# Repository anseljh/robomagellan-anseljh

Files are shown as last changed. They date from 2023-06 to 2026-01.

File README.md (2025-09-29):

# robomagellan-anseljh

This repo has notes, code, and other stuff related to my work toward competing in a Robo-Magellan contest. I plan to do at least the [TableBot challenge](https://github.com/anseljh/tablebot) first, but I've started planning and collecting parts for Robo-Magellan. I hope to be ready to compete in spring/summer 2024, but that may be overly ambitious. 2025 for sure!

## Robo-Magellan

> Robo-Magellan is a robotics competition emphasizing autonomous navigation and obstacle avoidance over varied, outdoor terrain. Robots have three opportunities to navigate from a starting point to an ending point and are scored on time required to complete the course with opportunities to lower the score based on contacting intermediate points.

- RoboGames [Robo-Magellan Rules](http://robogames.net/rules/magellan.php)
- Seattle Robotic Society Robothon [Robo-Magellan Rules](https://robothon.org/rules-robo-magellan/)

## Design Considerations

- **Size**: The robot will need to be able to overcome some terrain obstacles, so it shouldn't be too small or underpowered.
- **Sensors**:
  - GPS (navigation)
  - Compass (navigation; don't want to rely on GPS just to get heading)
  - Camera (to detect cones)
  - Distance sensors of some kind (collision avoidance)
  - Lidar (to detect cones; collision avoidance; also just cool)
  - Tactile sensors (to detect contact with cones)
- **Compute**:
  - Something powerful enough to process images from the camera and identify orange cones. I have a Raspberry Pi Model 3 A+ which I'll try out. It may be underpowered (only 512 GB RAM).
  - Planning to base the rest around an RP2040 board, probably one of my Raspberry Pi Picos. Could I just use the more powerful Raspberry Pi computer? Probably, but, among other considerations, I think it's more funny to make the computer be a peripheral for the microcontroller.
- **Dead man's switch**: The Robo-Magellan rules require the operator be able to stop a robot immediately by letting go of a switch. I have a few ideas about this, but nothing definitive. I might use the [RFM69HCW packet radios](https://www.sparkfun.com/products/12775) that I've used before and have a remote send a heartbeat to the robot while a button is pressed, and if that signal doesn't come, a relay cuts off power to the motors. I want to research how other people are doing this and maybe not reinvent the wheel. There's a Sparkfun tutorial called [How to Build a Remote Kill Switch](https://learn.sparkfun.com/tutorials/how-to-build-a-remote-kill-switch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) that is very similar to my concept.
- **Logging**: I'll want to log data for later analysis. I got an SD card breakout board for this that I haven't tried out yet. On the other hand, I might want to use that for quickly delivering GPS coordinates to the bot. Might need to get a second one in that case.

## Intermediate Milestones

1. **Do a working [TableBot](https://www.hbrobotics.org/index.php/challenges/).** Work on fundamentals in a small form factor. Complete a project of some complexity with CircuitPython. Fun!
1. **Make the remote.** Decide on the dead-man's switch mechanism. Design the PCB for the remote. Get it fabricated. Add panel-mount holes to an enclosure, including a port for the Wii Nunchuck. Attach all the things! Test it with the TableBot.
1. **Get the big DC motors running.** This entails working out all the power management for the motors, and hooking up the motor driver.
1. **Test remote motor power cut-off.** Need to verify this works before getting too far along with everything else.
1. **Figure out how to mount wheels to the big DC motors.** I'm even more of a rookie when it comes to mechanical engineering. Lots to learn here.
1. **Build a chassis.** Figure out how big & what kind of chassis to build. Build it.
1. **Do a working [FloorBot](https://www.hbrobotics.org/index.php/challenges/).** This is another good intermediate goal. I can use the same chassis, motors, remote, etc., but not have to worry about GPS, terrain, and recognizing orange cones yet.

## Parts Selection

### Motors

I got four chunky motors at a [Homebrew Robotics Club](hbrobotics.org/) meeting in early 2023. It's been a bit challenging to pin down precisely what they are, but I *think* they are [RAE M1500 permanent magnet DC motors](http://raemotors.com/products/motors/dc-motors/m1500-series/m1500.php) with [G211 right-angle gearmotors](http://raemotors.com/products/motors/gearmotors/right-angle/g211-series.php). Here are the basic specifications. I think they'll do the job.

- Voltage: 18V
- Current: 2A
- Speed: 200 rpm
- Torque: 6 in.-lb.
- Weight: Unknown. Need to weight them. Heavy!

### Battery & Power Distribution

Those motors will need a good amount of power. So far, I think I'll use a small-ish SLA battery. You can get one for about $20. I'll then need to step up the power from 12V to 18V, so I got a [Pololu 4.5-20V Fine-Adjust Step-Up Voltage Regulator U3V70A](https://www.pololu.com/product/2890).

### Chassis

I haven't thought about the chassis much yet. It needs to be able to hold these heavy motors and the SLA battery, which itself is 4.5 pounds.

### Motor Driver

The little motor drivers I've used before won't cut it for driving multiple 18V 2A motors, so I needed to get a beefier driver. I settled on the [Cytron 10A 5-30V Dual Channel DC Motor Driver](https://www.robotshop.com/products/cytron-10a-5-30v-dual-channel-dc-motor-driver?variant=42358540009633). I considered the very cool [RoboClaw](https://www.basicmicro.com/motor-controller) as shown in [Camp Peavy's book *HomeBrewed Robots!*](https://www.amazon.com/HomeBrewed-Robots-Camp-Peavy/dp/B0BW283Q27), but it's expensive and a bit more complex than I need. (I think.)

### Wheels, et cetera

I need to figure out how to mount wheels to the motor shafts, which are 1/4" diameter. I don't know much about this part. It seems to be hard to find wheel hubs for 1/4" diameter shafts, but there's probably stuff I'm missing.

### GPS

Thanks to a thread on the [Homebrew Robotics Club mailing list](https://groups.google.com/g/hbrobotics/about), I scored a GPS module for $9. It's the [HiLetgo GY-NEO6MV2](https://www.amazon.com/gp/product/B01D1D0F5M). It's not the best thing ever, but it works, and did I mention that it was $9? It uses a [Ublox NEO-6M](https://www.u-blox.com/en/product/neo-6-series) GPS module. It's 3V compatible and you just communicate to it over a UART. There's a [CircuitPython GPS library](https://docs.circuitpython.org/projects/gps/en/latest/) that works great. It takes several minutes to warm up (or whatever it's doing) but once that's done, it works fine.

### Lidar

I have a [getSurreal XV Lidar Sensor Mount Package](https://www.getsurreal.com/product/xv-lidar-sensor-mount-package/), which uses the lidar sensor from a Neato XV robotic vacuum.

The controller is the [getSurreal Lidar Controller v2.0](https://www.getsurreal.com/product/lidar-controller-v2-0/).

I had to get a replacement [drive belt](https://www.amazon.com/dp/B08KFNRXXV) for the motor that spins the laser around. ($9.95)

### Distance sensors

In addition to the lidar, I'm planning to add a few other distance sensors around the bot for further collision avoidance redundancy, in case something goes wrong with the lidar. I'm not sure yet how many distance sensors I want, or what type to use.

I have a trusty HC-SR04 ultrasonic sensor which uses 5V, as well as a 3.3V equivalent [RCWL-1601](https://www.adafruit.com/product/4007). These will probably work OK, but I'll need to test. I may need to get more depending on what kind of coverage I want.

[My TableBot](https://github.com/anseljh/tablebot) is using some [little infrared sensors](https://www.amazon.com/dp/B07W97H2WS) for detecting the edge of the table, but I doubt they'll be good for this application.

### Compute

I'd like to primarily use a Raspberry Pi Pico. The Pico is a cool little board based on the RP2040 microcontroller chip. I've been programming these in [CircuitPython](https://circuitpython.org/), and it is tons of fun.

There are two tasks that will require more compute power than the little Pico can muster, so I'm planning to use a beefier single-board computer for those tasks, and send their outputs to the Pico. So far I intend to use a Raspberry Pi Model 3 A+. It will process camera images to find the target cones, and send its conclusions to the Pico.

### Logging

I'll log telemetry to a micro SD card. I have a breakout board for that.

Should there be a realtime clock? Might not need one because we can [get time from the GPS](https://docs.circuitpython.org/projects/gps/en/latest/examples.html#time-source).

## Bills of Materials

### Control Board

- [ ] Custom PCB
- [x] Raspberry Pi Pico - $4
- [x] [RFM69HCW packet radio](https://www.sparkfun.com/products/12775) to receive dead-man's switch signal (autonomous mode) and commands from remote (manual mode) - $14
- [x] Antenna - $1
- [x] SMA antenna connector
- [ ] Toggle switch for autonomous/manual mode selection
- [ ] LEDs for autonomous/manual mode indication
- [x] Speaker for auditory output
- [x] GPS module: [HiLetgo GY-NEO6MV2](https://www.amazon.com/gp/product/B01D1D0F5M) - $9
- [x] Magnetometer (compass): [Sparkfun Micromag 3-axis magnetometer](https://www.sparkfun.com/products/retired/244) - $15.49 on eBay
- [x] [Micro SD card breakout board](https://www.adafruit.com/product/4682) for logging - $3.50
- [ ] Second [Micro SD card breakout board](https://www.adafruit.com/product/4682) for GPS coordinates - $3.50
- [ ] Bump switch for cone touch detection
- [x] 2x connectors for data from optical encoders (TE Connectivity part no. [3-640442-5](https://www.te.com/usa-en/product-3-640442-5.html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)) - $1.08
- [x] [MCP23008](https://www.adafruit.com/product/593) I2C GPIO expander - $1.95

### Motors and Drive System

- [x] 2x [RAE M1500 permanent magnet DC motors](http://raemotors.com/products/motors/dc-motors/m1500-series/m1500.php) with [G211 right-angle gearmotors](http://raemotors.com/products/motors/gearmotors/right-angle/g211-series.php) - free
- [x] 2x [Broadcom HEDM-5600#J06 optical encoders](https://www.broadcom.com/products/motion-control-encoders/incremental-encoders/transmissive-encoders/hedm-5600j06) - *requires 5V* - free
- [x] [Cytron 10A 5-30V Dual Channel DC Motor Driver](https://www.robotshop.com/products/cytron-10a-5-30v-dual-channel-dc-motor-driver?variant=42358540009633) - $23.50

### Power Systems

- [x] 12V SLA battery, like this [Mighty Max 12V 7 Ah SLA battery](https://www.homedepot.com/p/MIGHTY-MAX-BATTERY-12-Volt-7-Ah-Sealed-Lead-Acid-SLA-Rechargeable-Battery-ML7-12/307979135). It weighs 4.5 pounds. - $20
- [x] [Pololu 4.5-20V Fine-Adjust Step-Up Voltage Regulator U3V70A](https://www.pololu.com/product/2890): I'll use one of these to step up the 12V from the SLA battery to 18V to the motors. ([Bought from RobotShop](https://www.robotshop.com/products/pololu-45-20v-fine-adjust-step-up-voltage-regulator-u3v70a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)) - $40.95
- [x] Mini fuse holder: [Littelfuse FHM2BP](https://www.oreillyauto.com/detail/c/blister-pack/littelfuse-blister-pack-fuse-holder/lit3/fhm2bp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) - $4.99
- [x] 5A mini fuse: [Littelfuse 5 Amp Fuse MIN5BP](https://www.oreillyauto.com/detail/c/blister-pack/littelfuse-blister-pack-5-amp-fuse/lit3/min5bp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) - $5.29 for 5
- [ ] Big red button for emergency stop
- [ ] Toggle switch for control board power
- [ ] Toggle switch for manual motor power enable/cutoff
- [ ] Relay for motor power control
- [ ] Battery for control board
- [ ] 2x USB to micro-USB cable
  - Battery to Raspberry Pi 3 power
  - Raspberry Pi 3 to lidar controller

### Camera/Lidar System

- [x] Raspberry Pi Model 3 A+ - $25
- [x] Random old webcam (If it doesn't work well enough, get a Raspberry Pi Camera Module)
- [ ] Micro-USB cable from battery
- [x] [getSurreal Lidar Controller v2.0](https://www.getsurreal.com/product/lidar-controller-v2-0/) and [Mount Package](https://www.getsurreal.com/product/xv-lidar-sensor-mount-package/) with Neato XV lidar sensor

### Remote & Dead-Man's Switch

For the safety stop mechanism, I'm envisioning a small handheld device that will double as a remote control when moving the robot manually.

- [ ] Custom PCB
- [x] Raspberry Pi Pico - $4
- [x] [RFM69HCW packet radio](https://www.sparkfun.com/products/12775) - $14
- [x] Antenna - $1
- [x] SMA antenna connector
- [x] [Adafruit Wii Nunchuck Breakout Adapter](https://www.adafruit.com/product/4836) - $2.95
- [x] Wii Nunchuck
- [ ] Big button for dead-man's switch
- [ ] Toggle switch for power
- [ ] Enclosure (I have a few that might work)
- [ ] Green LED for connection indicator
- [ ] Red LED for heartbeat blink
- [ ] Another LED for mode indicator?

## Pins Required

### Control Pico

- 2 for UART to Pi 3
- 2 for UART to GPS module
- SPI (4) + 1 = **5** for radio
- SPI (3 reused + 1 CS) + 2 = **3** for magnetometer
- SPI (reuse 3 + 1 CS) + 1 = **2** for [Adafruit Micro SD SPI or SDIO Card Breakout](https://www.adafruit.com/product/4682)
- SPI (reuse 3 + 1 CS) + 1 = **2** for second SD card breakout
- 2x2 = **4** for optical encoders
- 1 for mode selection switch
- 1 for mode selection LED
- 1 for speaker
- 1 for bump switch
- 1 for motor power relay
- 4 for motor driver

Total: **29**

Uh-oh; there are only 26 usable GPIO pins on the Pico. We'll have to offload some of this to an IO expander. I have both an [MCP23008](https://www.adafruit.com/product/593) and an [MCP23017](https://www.adafruit.com/product/732) for that (I2C to 8 or 16 GPIO, respectively).

### Raspberry Pi 3

- 2 for UART to Pico

Total: **2**

### Remote Pico

- 1 for dead-man's switch
- 5 for radio
- 2 for I2C to Nunchuck breakout board
- 3 for indicator LEDs

Total: **11**

## Block Diagram

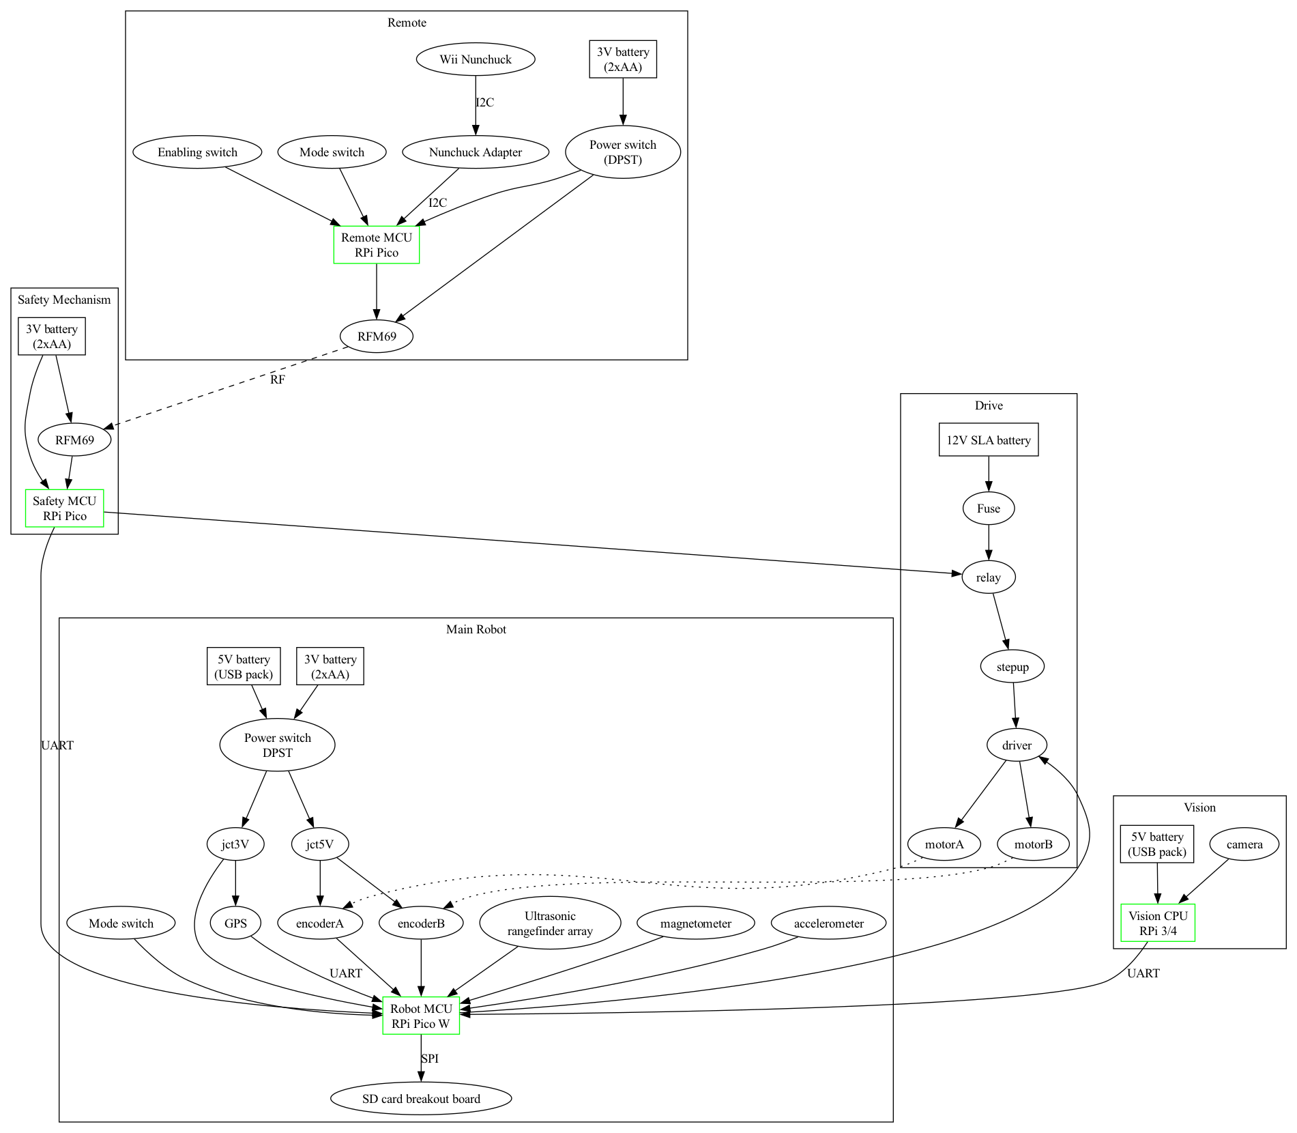
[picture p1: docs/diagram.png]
Diagram of systems and components


Rendered with [Graphviz](https://graphviz.org/) from `docs/diagram.dot` with:

```shell
dot -Tpng docs/diagram.dot > docs/diagram.png
```

## Software used

- [Graphviz](https://graphviz.org/) for block and state diagrams
- [LibreCAD](https://librecad.org/) for 2D CAD drawings, mainly for drilling templates for the chassis

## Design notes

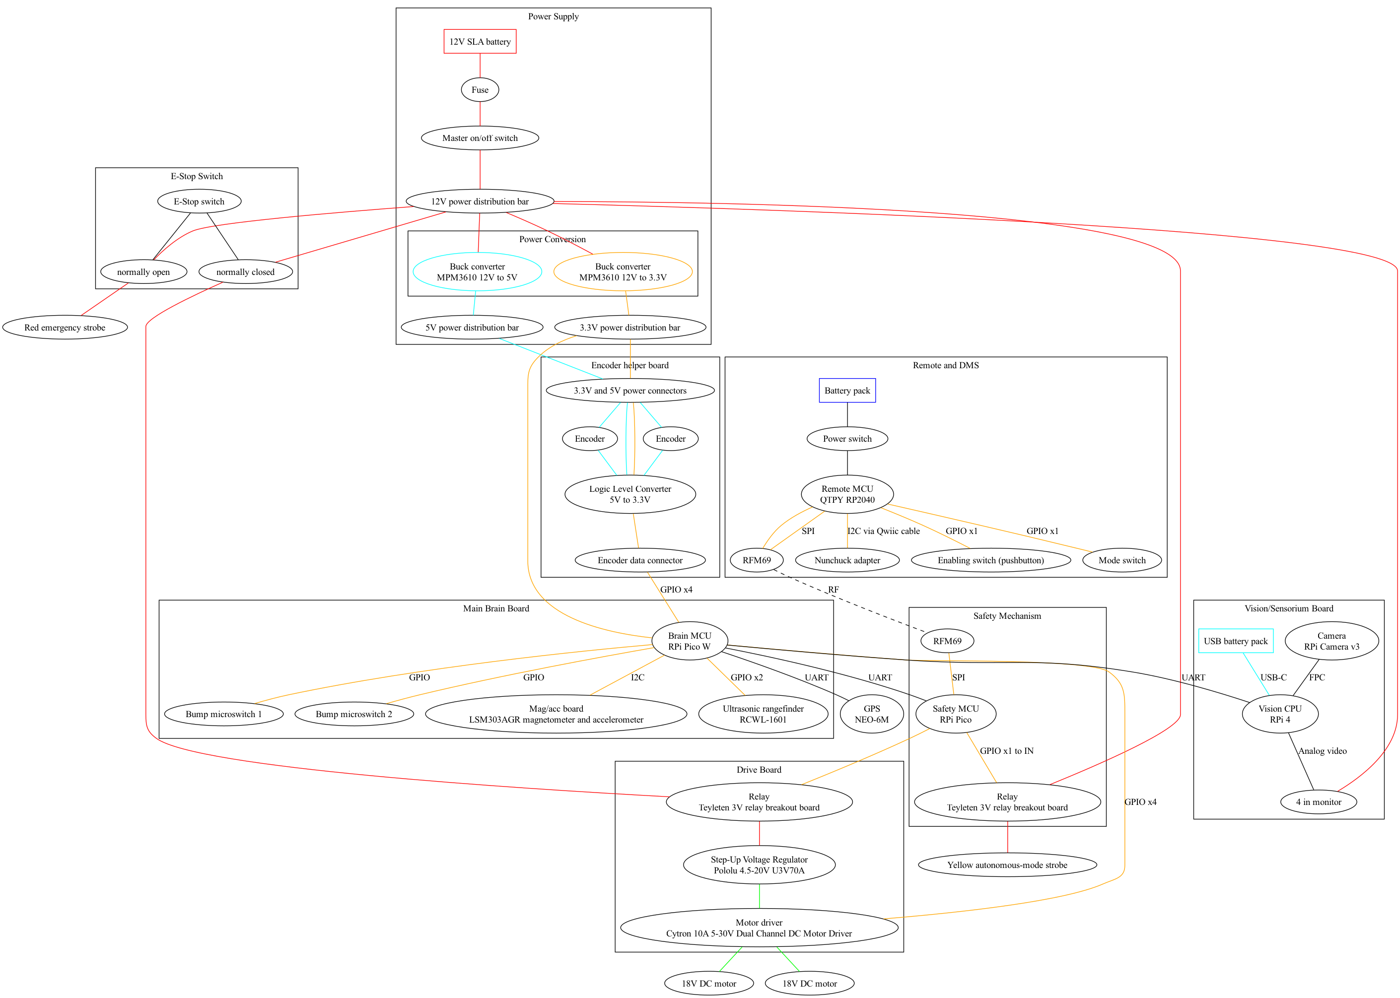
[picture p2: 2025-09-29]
docs/clanker-hardware.png

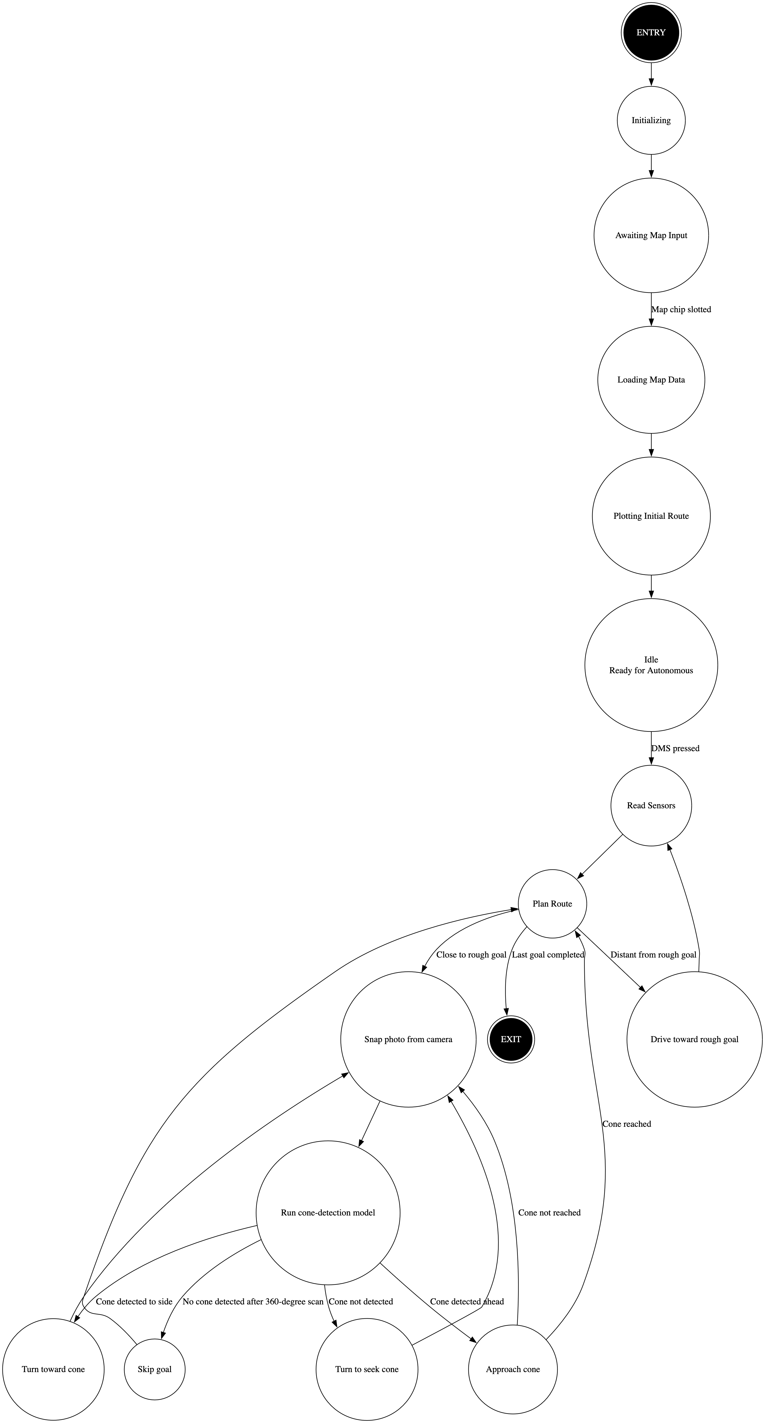
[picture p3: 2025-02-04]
docs/states.png

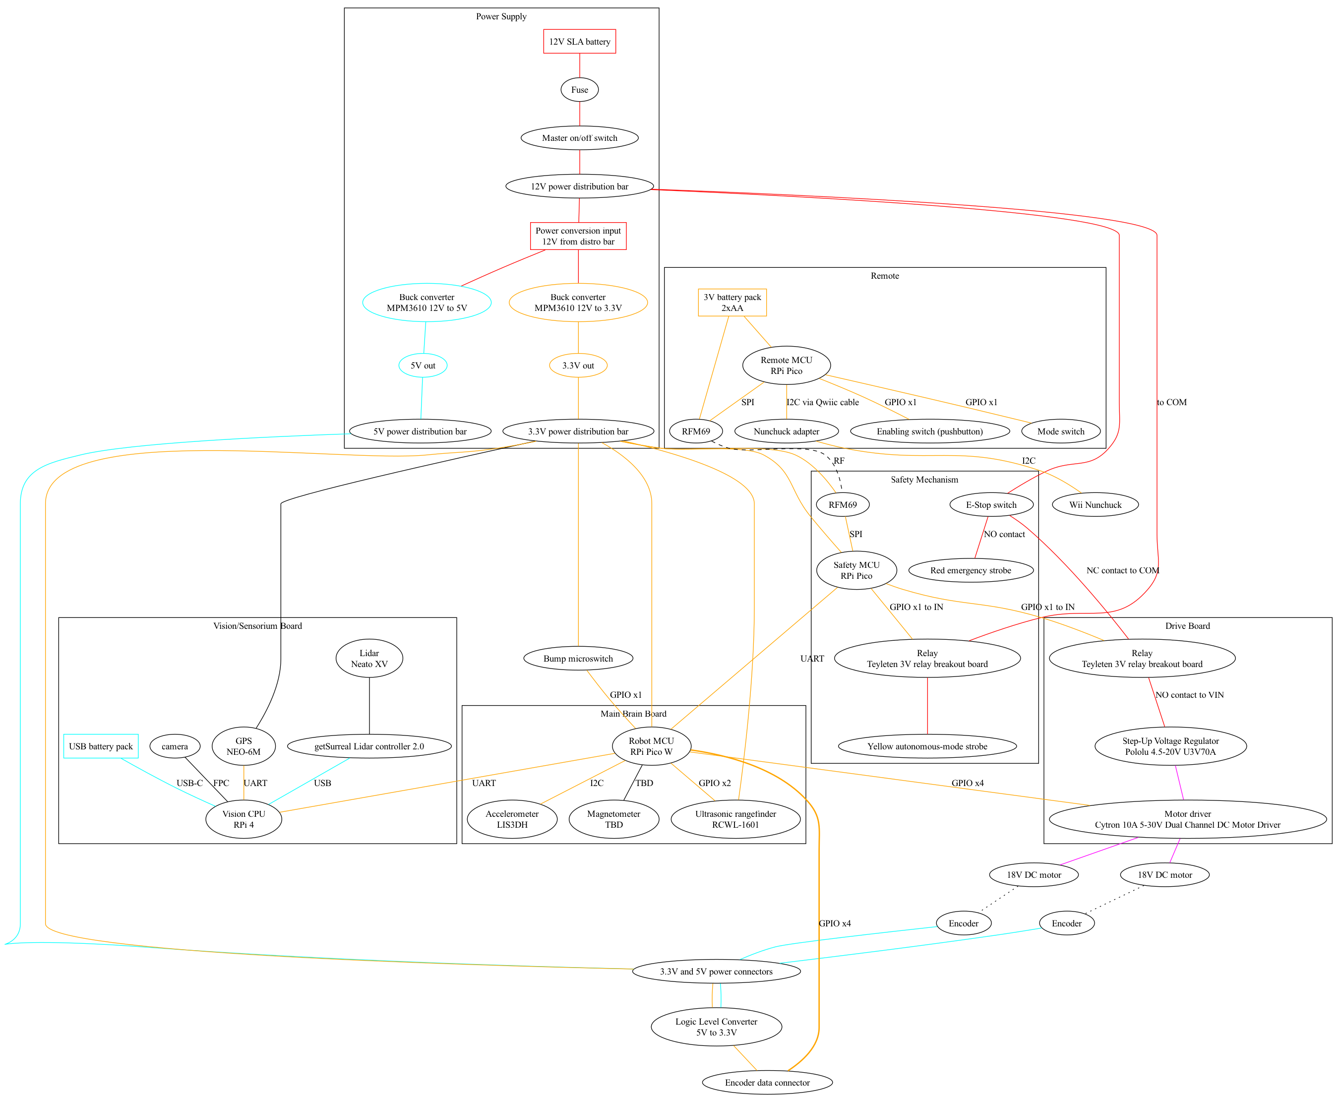
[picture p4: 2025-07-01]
docs/diagram3.png

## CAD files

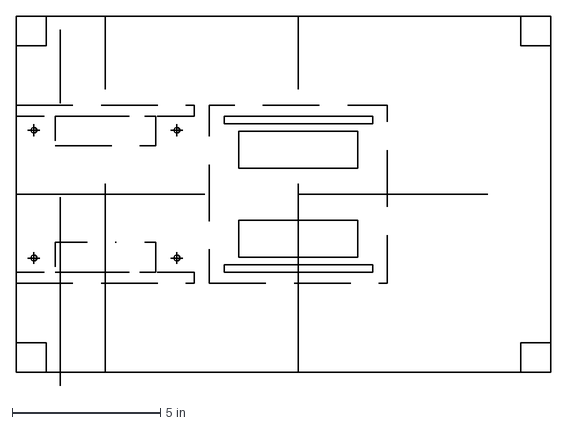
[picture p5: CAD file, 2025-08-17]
CAD/Lower MDF board.dxf
18.0 x 12.5 in

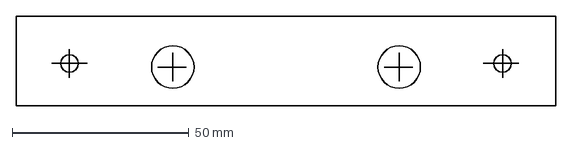
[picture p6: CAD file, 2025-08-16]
CAD/Bearing mount bar.dxf
152.4 x 25.4 mm

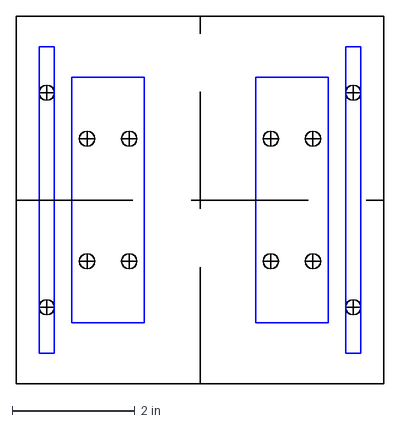
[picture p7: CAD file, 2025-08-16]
CAD/Motor mount plate.dxf
6.00 x 6.00 in

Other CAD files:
CAD/Empty template.dxf

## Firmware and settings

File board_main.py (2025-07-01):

"""
CircuitPython code for the main robot MCU.
Board: Raspberry Pi Pico W

Devices:
- Serial to safety board (hardware UART)
- Serial to vision RPi 4 (hardware UART)
- Serial to GPS module (PIO UART)
- (maybe) Serial to Neato lidar (PIO UART)
- Motor controller (4 GPIO pins)
- Mode selector switch (1 GPIO)
- Wifi network selector DIP switch (1 GPIO)
- Some status LEDs TBD (1 GPIO each)

Pinout diagram: https://picow.pinout.xyz/
"""

import time
import board
import pwmio
import digitalio
import busio

from utils import init_hw_uart, init_pio_uart
from robot import RoboMagellanBot

# Pin setup
MODE_SELECTOR_PIN = None # mode-selector switch (manual / autonomous)
AUTONOMOUS_LAMP_PIN = None # bright yellow light or strobe to indicate autonomous mode is active
VISION_TX_PIN = None
VISION_RX_PIN = None
GPS_TX_PIN = None
GPS_RX_PIN = None
LIDAR_TX_PIN = None
LIDAR_RX_PIN = None
M1_PWM_PIN = None
M1_DIR_PIN = None
M2_PWM_PIN = None
M2_DIR_PIN = None
QWIIC_SCL = None
QWIIC_SDA = None

class Motor:
    FORWARD = 1
    BACKWARD = -1
    
    def __init__(self, pwm_pin, dir_pin, motor_dir=FORWARD):
        self.pwm = pwmio.PWMOut(pwm_pin, frequency=1000, duty_cycle=0)
        self.dir = digitalio.DigitalInOut(dir_pin)
        self.dir.direction = digitalio.Direction.OUTPUT

    def set_speed(self, speed):
        if speed < 0:
            self.dir.value = True
            self.speed = -speed
        else:
            self.dir.value = False
            self.speed = speed
        
        # Flip direction if motor is facing opposite
        if self.motor_dir == Motor.BACKWARD:
            self.dir.value = not self.dir.value
        
        self.pwm.duty_cycle = int(self.speed * 65535)
    
    def stop(self):
        self.pwm.duty_cycle = 0

class Drivetrain:
    def __init__(self, M1_PWM_PIN, M1_DIR_PIN, M2_PWM_PIN, M2_DIR_PIN):
        self.motor_left = Motor(M1_PWM_PIN, M1_DIR_PIN, Motor.FORWARD)
        self.motor_right = Motor(M2_PWM_PIN, M2_DIR_PIN, Motor.BACKWARD)
        self.stop()
        print("Drivetrain reporting for duty!")

    def stop(self):
        self.motor_left.stop()
        self.motor_right.stop()
    
    def turn_left(self, speed):
        self.motor_left.set_speed(-speed)
        self.motor_right.set_speed(speed)

    def turn_right(self, speed):
        self.motor_left.set_speed(speed)
        self.motor_right.set_speed(-speed)
    
    def forward(self, speed):
        self.motor_left.set_speed(speed)
        self.motor_right.set_speed(speed)

    def backward(self, speed):
        self.motor_left.set_speed(-speed)
        self.motor_right.set_speed(-speed)
    
    def test_partern(self):
        self.stop()
        
        # TODO: Honk
        time.sleep(1)
        
        self.turn_right(0.25)
        time.sleep(1)
        self.stop()
        time.sleep(1)
        
        self.turn_left(0.25)
        time.sleep(1)
        self.stop()
        time.sleep(1)
        
        self.forward(0.25)
        time.sleep(1)
        self.stop()
        time.sleep(1)
        
        self.backward(0.25)
        time.sleep(1)
        self.stop()
        
        # TODO: Honk

class MainBoard:

    def __init__(self):
        # UART from safety MCU for conveying non-safety commands from remote
        self.uart_safety = init_hw_uart(board.TX, board.RX)

        # UART for cone prediction from RPi 4
        self.uart_vision = init_pio_uart(VISION_TX_PIN, VISION_RX_PIN)

        # UART for GPS module
        self.uart_GPS = init_pio_uart(GPS_TX_PIN, GPS_RX_PIN)
        
        # UART for Neato lidar
        # self.uart_lidar = None # TODO: setup a PIO UART for the Neato lidar
        # self.uart_lidar = init_pio_uart(LIDAR_TX_PIN, LIDAR_RX_PIN)

        # Initialize drivetrain
        self.drivetrain = Drivetrain()

        # Init mode selector switch
        # TODO

        # Init I2C bus for Qwiic devices
        i2c1 = busio.I2C(QWIIC_SCL, QWIIC_SDA)

        self.bot = RoboMagellanBot()

    def main_loop():
        pass

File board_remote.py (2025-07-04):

"""
CircuitPython code for the remote MCU.
Board: Adafruit QT PY RP2040
    https://circuitpython.org/board/adafruit_qtpy_rp2040/

Devices:
- RFM69 radio (SPI)
- Nunchuk adapter (I2C)
- Dead-man's switch button (1 GPIO)
- Autonomous/manual selector switch (1 GPIO)
- Autonomous-mode LED (1 GPIO)

Sparkfun: How to Build a Remote Kill Switch
    https://learn.sparkfun.com/tutorials/how-to-build-a-remote-kill-switch
"""

import time
import board
import busio
from digitalio import DigitalInOut, Direction, Pull

from adafruit_nunchuk import Nunchuk

from utils import init_radio

# Pin setup
PIN_MOSI = board.GP3
PIN_MISO = board.GP4
PIN_SCK = board.GP6
PIN_CS = board.GP5
PIN_RESET = board.GP20
QWIIC_SCL = board.GP23
QWIIC_SDA = board.GP22
SWITCH_DEAD_MAN = board.A0  # A0 for enabling/dead-man's switch
SWITCH_MODE = board.A1  # A1 for autonomous/manual mode switch
# nothing on A2 yet
LED_MODE = board.A3  # A3 for autonomous/manual mode LED


class RemoteBoard:
    def __init__(self):
        # Init mode LED
        self.led_mode = DigitalInOut(LED_MODE)
        self.led_mode.direction = Direction.OUTPUT
        print("Mode LED initialized.")

        # Init mode switch
        self.switch_mode = DigitalInOut(SWITCH_MODE)
        self.switch_mode.direction = Direction.INPUT
        # self.switch_mode.pull = None  # Pull.UP  # Pull-up resistor for switch
        print("Mode switch initialized.")

        # Init dead-man's switch
        self.switch_enabling = DigitalInOut(SWITCH_DEAD_MAN)
        self.switch_enabling.direction = Direction.INPUT
        # self.switch_enabling.pull = Pull.UP
        print("Dead-man's switch initialized.")

        # Init RFM69 radio
        self.radio = init_radio(
            mosi_pin=PIN_MOSI,
            miso_pin=PIN_MISO,
            clock_pin=PIN_SCK,
            cs_pin=PIN_CS,
            reset_pin=PIN_RESET,
        )
        print("RFM69 radio initialized.")
        print(self.radio)
        print(f"Temperature: {self.radio.temperature}C")
        print(f"Frequency: {self.radio.frequency_mhz} MHz")
        print(f"Bit rate: {self.radio.bitrate / 1000} kbit/s")
        print(f"Frequency deviation: {self.radio.frequency_deviation} Hz")

        # Instantiate Nunchuck
        i2c1 = busio.I2C(QWIIC_SCL, QWIIC_SDA)
        try:
            self.nunchuck = Nunchuk(i2c1)
            print("Nunchuk initialized.")
            print(self.nunchuck)
        except ValueError as e:
            print(f"Failed to initialize Nunchuk: {e}")
            self.nunchuck = None
        
        print("** Remote board initialized **")

    def main_loop(self):
        print("Remote main loop beginning...")
        while True:
            if self.switch_mode.value:
                print("Mode switch is HIGH")
                self.led_mode.value = True
                print("Autonomous mode active.")
            else:
                print("Mode switch is LOW")
                self.led_mode.value = False
                print("Manual mode active.")

            print(f"Enabling switch: {self.switch_enabling.value}")

            # Read the Nunchuk state
            if self.nunchuck:
                print(f"Nunchuk state: stick {self.nunchuck.joystick} / buttons {self.nunchuck.buttons} / accel {self.nunchuck.acceleration}")

            time.sleep(0.5)


if __name__ == "__main__":
    board = RemoteBoard()
    for _ in range(3):
        board.led_mode.value = True
        time.sleep(0.5)
        print("Blinking")
        board.led_mode.value = False
        time.sleep(0.5)
    board.main_loop()

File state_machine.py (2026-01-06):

from time import monotonic, sleep


class State:
    def __init__(self, name: str):
        self.name = name
        self.transitions = {}
    
    def run(self, machine):
        pass


class StateMachine:

    def __init__(self, initial_state: State | None = None):
        self.state = initial_state
        self.states = {}
        self.transition_table = {}

    def add_state(self, state: State):
        self.states[state.name] = state
    
    def add_transition(self, from_state: State, to_state: State, evaluator_fn):
        from_state.transitions[to_state.name] = evaluator_fn
        
        # self.transition_table[(from_state.name, evaluator_fn)] = to_state
        if from_state.name not in self.transition_table:
            self.transition_table[from_state.name] = {}
        self.transition_table[from_state.name][to_state.name] = evaluator_fn
    
    def enter(self, state: State):
        print(f"Entering state '{state.name}'")
        self.last_transition_time = monotonic()
        self.state = state
        # self.state.run(self)
    
    def exit(self, state: State):
        print(f"Exiting state '{state.name}'")


class RobotStateMachine(StateMachine):

    def __init__(self):
        super().__init__()
        self.robot_name = "Clanker"
        self.start_time = monotonic()
        self.last_transition_time = None
        
        self.init_done = False
        self.map_data = []
        self.stop_condition = False

        initializing_state = InitializingState("initializing")
        print(initializing_state)
        awaiting_map_state = AwaitingMapState("awaiting_map")
        mission_accomplished_state = MissionAccomplishedState("mission_accomplished")

        self.add_state(initializing_state) #, self.initialize)
        self.add_state(awaiting_map_state)
        self.add_state(mission_accomplished_state)
        self.add_transition(initializing_state, awaiting_map_state, self.is_init_done)
        self.add_transition(awaiting_map_state, mission_accomplished_state, self.is_map_loaded)

        self.enter(initializing_state)


    def loop(self):
        while not self.stop_condition:
            print(monotonic() - self.start_time)
            next_state = None
            self.state.run(self)

            from_state = self.state.name
            if from_state in self.transition_table:
                for to_state in self.transition_table[from_state]:
                    evaluator_fn = self.transition_table[from_state][to_state]
                    if evaluator_fn():
                        next_state = self.states[to_state]
                        break

            if next_state:
                self.exit(self.state)
                self.enter(next_state)
                self.state.run(self)
            sleep(1)
        print("loop() done!")

    def is_init_done(self):
        print("is_init_done()")
        if self.init_done:
            print("yes")
            return True
        else:
            print("no")
            return False

    def is_map_loaded(self):
        print("is_map_loaded()")
        if self.map_data is not None:
            print("yes")
            return True
        else:
            print("no")
            return False
    
    def hello(self):
        print(f"Hello! I am {self.robot_name}.")


class InitializingState(State):
    def run(self, machine: RobotStateMachine):
        print(f"Initializing...")
        print("beep")
        print("boop")

        if monotonic() - machine.start_time > 5:
            machine.init_done = True
            print("Done initializing")
            machine.hello()
        

class AwaitingMapState(State):
    def run(self, machine: RobotStateMachine):
        print(f"Awaiting map...")
        print("beep")
        print("boop")
        if machine.last_transition_time and monotonic() - machine.last_transition_time > 5:
            machine.map_data = [
                (1, 2, "start"),
                (3, 4, "cone"),
                (5, 6, "end"),
            ]
            print(f"Got a map! {machine.map_data}")


class MissionAccomplishedState(State):
    def run(self, machine: RobotStateMachine):
        machine.stop_condition = True
        print(f"Mission accomplished!!!")

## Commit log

2023-05-24 Parts update; SD card thoughts
    - Got 12V battery, fuse holder, and fuses
    - More thought on SD cards
2025-07-01 Updates to remote, safety, and main boards per latest hardware decisions
2025-07-04 Checkpoint on remote board. Not quite working yet.
2025-08-16 Add 2D CAD drawings
    [Bearing mount bar.dxf, Motor mount plate.dxf]
2025-08-17 Add big CAD drawing for lower MDF board
    [Empty template.dxf, Lower MDF board.dxf]
